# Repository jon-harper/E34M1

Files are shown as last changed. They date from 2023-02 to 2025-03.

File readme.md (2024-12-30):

Welcome to the E34M1 repository! E34M1 adapts the [EVA 3](https://main.eva-3d.page/) toolhead for the [ZeroG Mercury One](https://docs.zerog.one/) project.

This repository stores the core files for E34M1 and a number of mods. Note that many mods are published on Printables or elsewhere. A full list is available in the **[E34M1 Documentation](https://jon-harper.github.io/E34M1/)**.

## Quick Links

- [Tour](https://jon-harper.github.io/E34M1/tour/)
- [Modules & BOM](https://jon-harper.github.io/E34M1/modules/)
- [Assembly Guide](https://jon-harper.github.io/E34M1/assembly/)

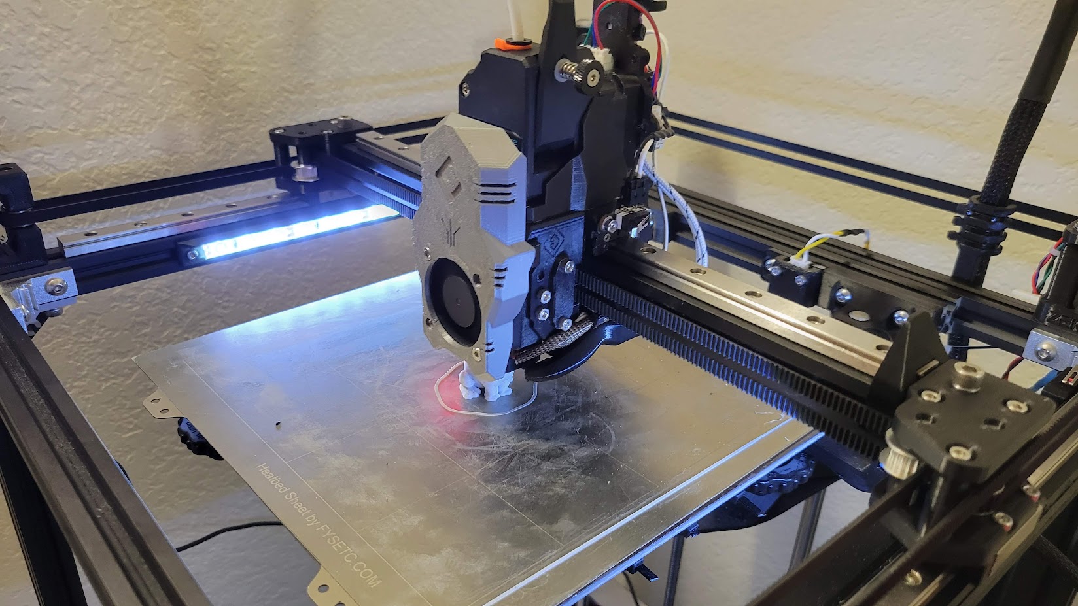
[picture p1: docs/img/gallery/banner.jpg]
E34M1 printing


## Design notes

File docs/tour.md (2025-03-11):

---
title: Visual Tour
summary: E34M1 Modules Tour
authors: Jon Harper
date: 2023-1-26
---

## Overview

Hotends, extruders, and most shrouds are compatible between EVA 3 and E34M1, but the core components of the toolhead are different. This tour introduces E34M1 and the larger EVA 3 ecosystem.

<div markdown class="grid">
<div markdown class="card">

**Core E34M1 Assembly**
<figure markdown>
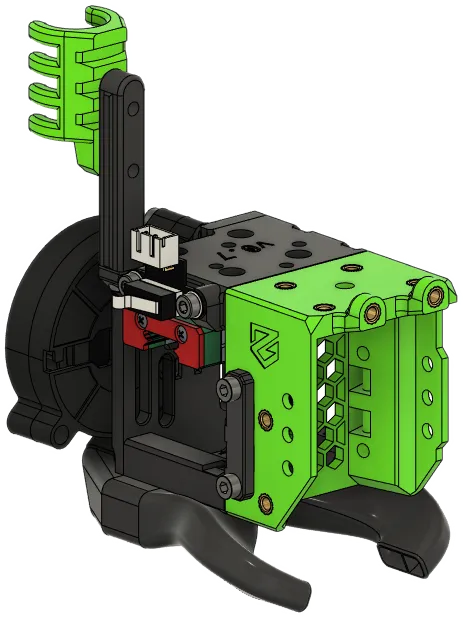
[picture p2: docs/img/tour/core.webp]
core

</figure>
</div>
<div markdown class="card">
**Complete Assembly**
<figure markdown>
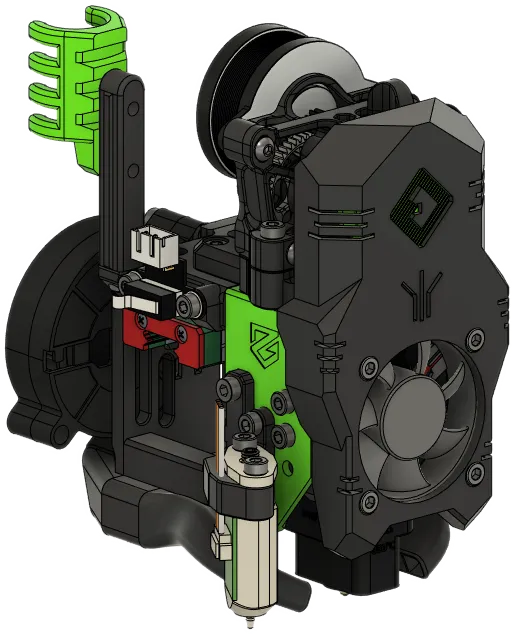
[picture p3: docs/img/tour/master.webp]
complete

</figure>
</div>
</div>

## Core Modules

Core modules are specific to E34M1. Each module comes in several variations.

<div markdown class="grid">
<div markdown class="card">

### [Front](modules/front.md)

The Front mounts the hotend, belts, the front of the Drive module, and optionally, an ABL method and/or accelerometer.

<figure markdown>
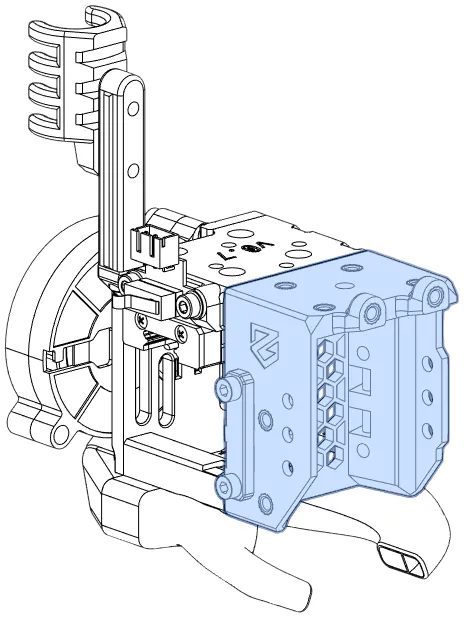
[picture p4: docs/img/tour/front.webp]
front

</figure>

</div>
<div markdown class="card">

### [Top](modules/top.md)

The top mounts the MGN12H carriage, the X endstop, and the back of the Drive module. Some Top modules have a cable guide attachment point.

<figure markdown>
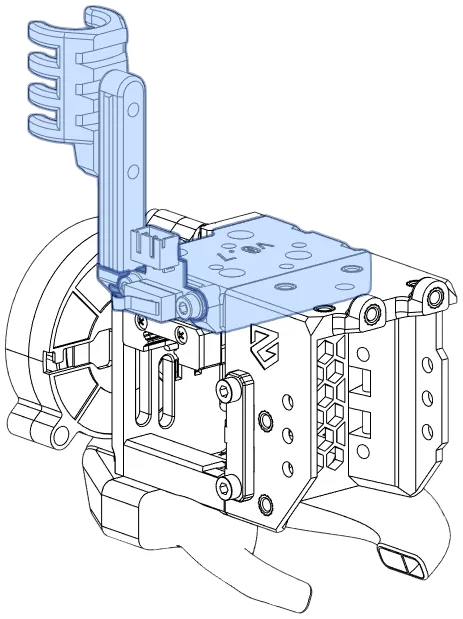
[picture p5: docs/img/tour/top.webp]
top

</figure>

</div>
<div markdown class="card">

### [Bottom Horns](modules/bottom.md)

The bottom horns form the lower joint between the Front and Rear Inlet; the horns direct part cooling air to the hotend nozzle. Some ABL methods (e.g., Beacon, Klicky) mount on the Bottom Horns.

<figure markdown>
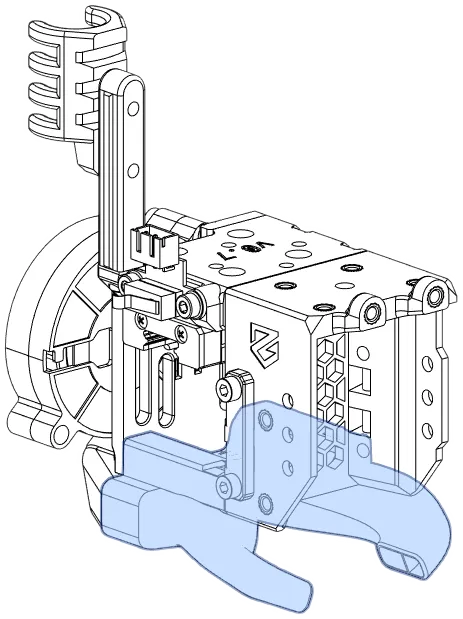
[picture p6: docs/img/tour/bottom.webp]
bottom

</figure>
</div>
<div markdown class="card">

### [Rear Inlet](modules/rear.md)

E34M1's rear body is much smaller than EVA3, and serves as a cooling fan inlet/mount.

<figure markdown>
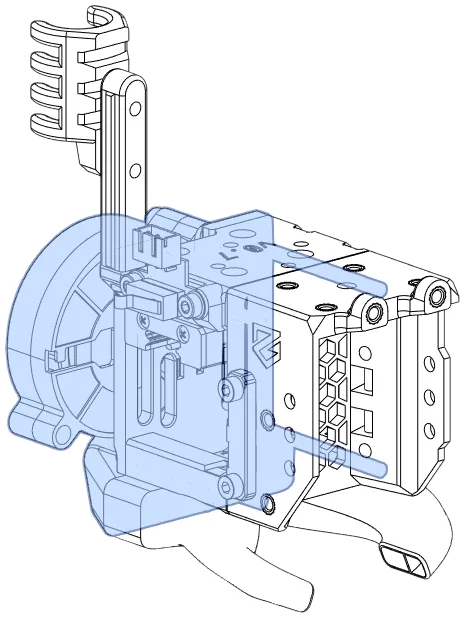
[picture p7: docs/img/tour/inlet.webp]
inlet

</figure>
</div>
<div markdown class="card">

### [ABL Side Mounts](modules/abl.md)

Some ABL methods mount here (e.g., BLTouch and CR Touch); this configuration is not compatible with EVA 3 ABL mounts.

<figure markdown>
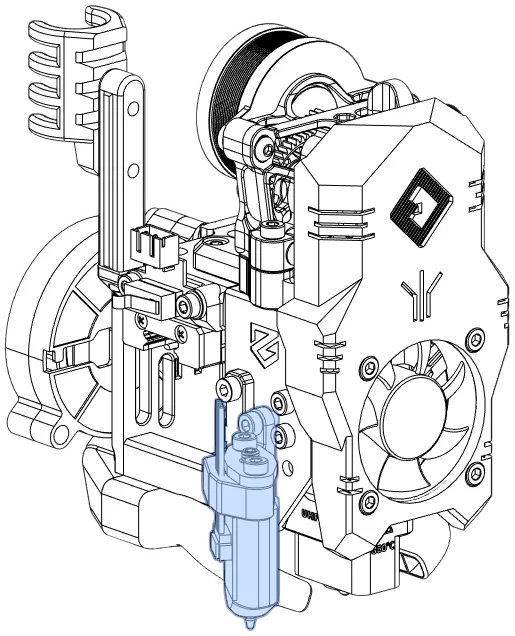
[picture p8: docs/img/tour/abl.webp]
abl mount

</figure>
</div>
</div>

## EVA-Compatible Modules

These modules are drop-in compatible with EVA 3.

<div markdown class="grid">
<div markdown class="card">

### [Hotends](modules/hotend.md)

The Hotend module mounts the hotend, cooling fan, and an optional shroud.

<figure markdown>
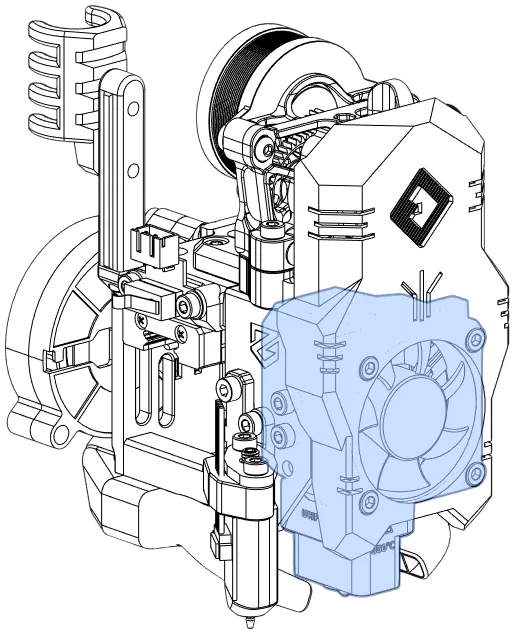
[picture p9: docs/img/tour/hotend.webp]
hotend

</figure>

</div>
<div markdown class="card">

### [Drives/Extruders](modules/drive.md)

The drive module attaches the extruder to the toolhead.

<figure markdown>
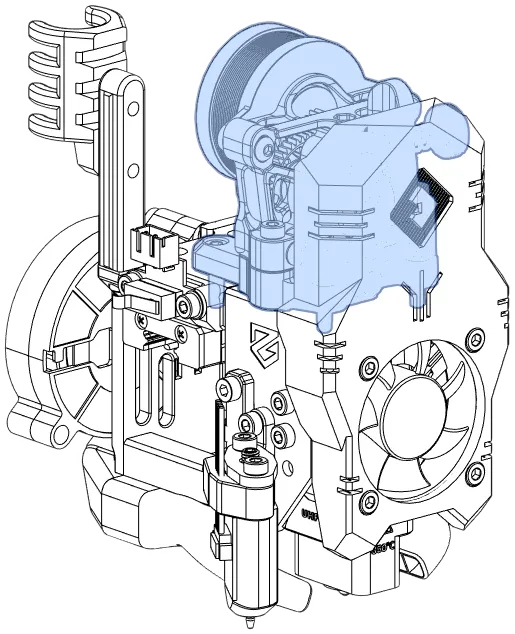
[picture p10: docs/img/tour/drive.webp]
drive

</figure>

</div>
<div markdown class="card">

### Shrouds

All stock EVA 3 shrouds are compatible with E34M1.

<figure markdown>
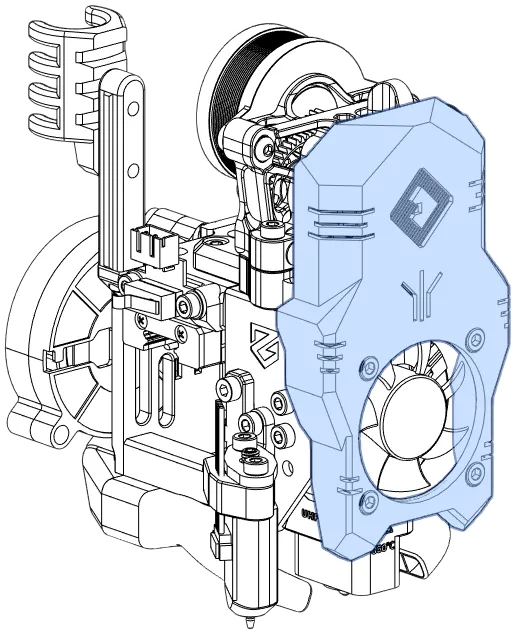
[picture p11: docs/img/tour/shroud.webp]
shroud

</figure>
- [Stock EVA 3 Shrouds](https://main.eva-3d.page/heat_insert/shrouds/chonkier/)
- [cuiviemen's Chonky Shrouds with LED Lighting](https://www.printables.com/model/420929-eva-30-chonky-shrouds-with-led-lighting)
</div>
</div>

## Other Components

E34M1 provides several other components that may be useful:

- [X Axis Stop Blocks](modules/stop_block.md): Bumpers for the X axis endstop.
- [NEMA17 PCB Mounts](modules/pcb_mounts.md): (Deprecated) NEMA17 steppers mounts for toolhead PCBs and shrouds to cover them.
- [Optional/Build-Specific](modules/other.md): Filament sensors, Klicky Docks, and other links.

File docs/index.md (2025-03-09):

---
title: The E34M1 Toolhead
summary: E34M1 landing page
authors: Jon Harper
date: 2023-1-26
hide: navigation toc
prefix: ''
---

<figure markdown class="jh-cover-img">
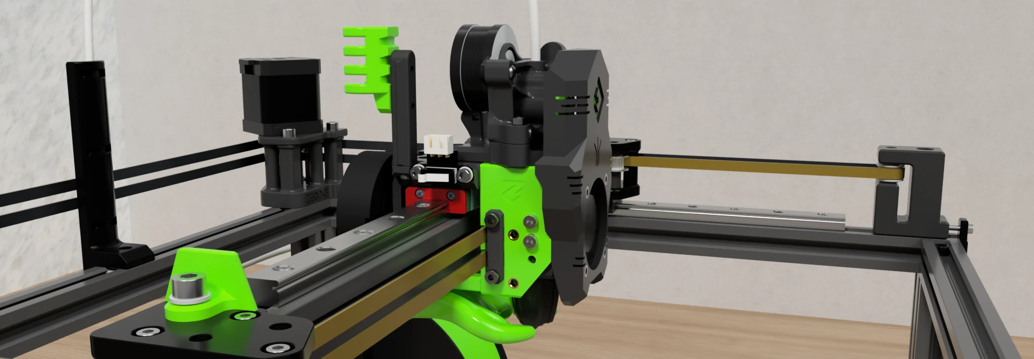
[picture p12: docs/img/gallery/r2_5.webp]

<figcaption markdown>
*E34M1 adapts the [EVA 3][eva3] toolhead
<br/> for [Mercury One.1][merc1]-based 3D printers.*
</figcaption>
</figure>

<div markdown class="grid">
<div markdown class="card">
### [:material-book-open: Introduction to E34M1](guide.md)

Overview of the toolhead and this documentation.
</div>
<div markdown class="card">
### [:material-directions: Visual Tour](tour.md)

Explore the toolhead and how it fits together.
</div>
<div markdown class="card">
### [:octicons-list-ordered-24: Sourcing Guide](sourcing.md)

Links to aid in locating and pricing parts.
</div>
<div markdown class="card">
### [:material-text-box-search-outline: Module Reference](modules/index.md)

Components, bills of materials, and notes.
</div>
<div markdown class="card">
### [:material-hammer-screwdriver: Assembly Guide](assembly/index.md)

Video and step-by-step instructions.
</div>
<div markdown class="card">
### [:octicons-log-24: Changelog](changelog.md)

What's new?
</div>
</div>

<div markdown class="grid">
<div markdown>
### License

E34M1, like [EVA 3][eva3], is licensed under the [Creative Commons BY-NC-SA 4.0 License](https://creativecommons.org/licenses/by-nc-sa/4.0/).

### Credits

E34M1 is a fork of [EVA 3][eva3] by [Paweł Kucmus](https://github.com/pkucmus). A community of makers supports E34M1, but special thanks go to [cuiviemen](https://www.printables.com/@cuiviemen_127292) and [Psych0h3ad](https://www.printables.com/@Psych0h3ad_168275) for their ideas, mod designs, testing, and feedback during development. Likewise, the testing and feedback from members of the [ZeroG Discord](https://discord.io/zerog) is invaluable.

### [:simple-kofi: Donations/Tip Jar](https://ko-fi.com/jonspaceharper)

E34M1 is free, but my Fusion 360 subscription and filament are not. Every donation helps! :material-heart:{.jh-red} *- Jon*
</div>
<div markdown>
<figure markdown class="jh-cover-img">
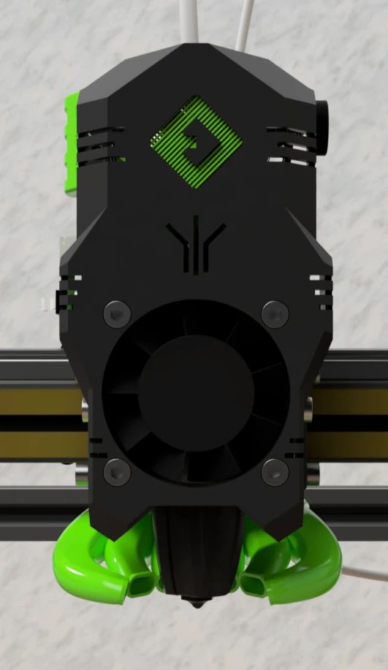
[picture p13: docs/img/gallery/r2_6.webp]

</figure>
</div>
</div>

[eva3]: https://main.eva-3d.page/
[merc1]: https://docs.zerog.one/

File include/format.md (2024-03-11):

{% import 'badges.md'as badges -%}

{% macro part_header(part_id, name) -%}
 {{ name }}
{% endmacro -%}

{% macro add_image(obj, img_width="240px", prefix = '') -%}
{% if obj.img_url -%}
{% set url = prefix + obj.img_url -%}
[{{obj.name}}}" }]({{url}})
{% endif -%}
{% endmacro -%}

{% macro add_figure(obj, img_width="240px", prefix = '') -%}
{% if obj.img_url -%}
{% set url = prefix + obj.img_url -%}
<figure markdown>
[{{obj.name}}}" }]({{url}})
</figure>
{% endif -%}
{% endmacro -%}

{%- macro add_note(comp) -%}
{% if comp.note -%}
{{ comp.note }}
{% else -%}
*(None)*
{% endif -%}
{% endmacro -%}

{%- macro add_hsi_info(item, img_width="200px", prefix='')-%}
{%- if 'hsi_img' in item.attributes.keys() %}
??? hsi "Heat Set Insert Locations"
    <div markdown class="grid">
{% for url in item.attributes['hsi_img'] %}
    [Heat set insert details}"}]({{prefix + url}})
{% endfor %}
    </div>
{% endif -%}
{%- endmacro -%}

{% macro comp_entry(comp, img_width="240px", prefix='') -%}
### {{ comp.name }}

{% if comp.attributes and comp.attributes['fit_test'] -%}

{{issue_tag(comp.attributes['fit_test'])}}
{% endif -%}

{% if comp.variants | count > 1 %}
{%- set indent='    ' -%}
{% for v in comp.variants -%}
=== "{{ v.name }}"
{{indent}}<div markdown class="grid"><div markdown>
{{indent}}{{ badges.render(comp, v, prefix=prefix) }}
{{indent}}
{{indent}}:octicons-paperclip-24: **General Notes**
{{indent}}
{{ make_indented(add_note(comp), indent) }}
{% if v.note -%}
{{indent}}:material-text-box-multiple-outline: **Variant Notes**
{{indent}}
{{ make_indented(add_note(v), indent) }}
{%- endif %}
{{indent}}</div><div markdown>
{{make_indented (add_figure(comp, img_width, prefix), indent) }}
{{indent}}</div></div>
{{indent}}:octicons-pencil-24: **Materials**
{{indent}}
{{ make_indented(bom_table(v, prefix=prefix), indent) }}
{{ make_indented(add_hsi_info(v, "200px", prefix), indent)}}
{%- endfor -%}
{%- else -%} {# comp.variants | count > 1 #}
{%- set v = comp.variants[0] -%}
<div markdown class="grid"><div markdown>
{{ badges.render(comp, v, prefix=prefix) }}

:octicons-paperclip-24: **General Notes**

{{ add_note(comp) }}

{% if v.note -%}
:material-text-box-multiple-outline: **Variant Notes**

{{add_note(v)}}
{%- endif %}
</div>
<div markdown>
{{ add_figure(comp, img_width, prefix) }}
</div>
</div>

:octicons-pencil-24: **Materials**

{{ bom_table(v, prefix=prefix) }}
{{ add_hsi_info(v, "200px", prefix) }}
{% endif -%} {# comp.variants | count > 1 #}

---------
{% endmacro -%}

{% macro source_table(part) -%}
| Source | Ships To | Ships From | Note |
|---|---|---|---|
{% if part.sources | count == 0 -%}
| | | |
{% else -%}
{% for source in part.sources -%}
| [{{source.supplier.name}}]({{source.url}} "{{source.supplier.name}}: {{part.name}}") | {{ source.supplier.ships }} | {{ source.supplier.region }} | {{ source.note }} |
{% endfor -%}
{% endif -%}
{% endmacro -%}

{% macro bom_table(variant, prefix='') -%}
| Type | Part | Qty |
|---|---|-----|
{% if variant.parts -%}
{% for part_id, qty in variant.parts.items()-%}
{% set part = product.partFromId(part_id) -%}
{% set link = part_link(part_id, part, prefix=prefix) -%}
{% if part.part_type == 'Printed' -%}
|:material-printer-3d-nozzle: {{part.part_type}}|{{link}}|{{qty}} {{part.units}}|
{% else -%}
|{{part.part_type}}|{{link}}|{{qty}} {{part.units}}|
{% endif -%}
{% endfor -%}
{% endif %}
{% endmacro -%}

{# I hate the way this macro is written, but a more concise version has newlines. #}
{% macro part_link(part_id, part = None, prefix = '', url_text=None) -%}
{% if not part -%}
{% set part = product.partFromId(part_id=part_id) -%}
{% endif -%}
{% if not url_text -%}
{% set url_text = part.name -%}
{% endif -%}
{% if not part.file_url and not part.sources -%}
{{url_text}}{% else -%}
{% if part.part_type == 'Printed' and part.file_url -%}
{% if part.file_url.startswith(product.local_url_prefix) -%}
{% set icon = ":material-git:" -%}
{% set url = part.file_url -%}
{% set tooltip = "E34M1 GitHub file download"-%}
{% else -%}
{% set icon = ':octicons-link-external-24:' -%}
{% set url = part.file_url -%}
{% set tooltip = 'External site file download'-%}
{% endif -%}
{% elif part.sources -%}
{% set icon = ':material-cart:' -%}
{% set url = prefix + 'sourcing.md#' + part_id -%}
{% set tooltip =  'Sourcing information' -%}
{% endif -%}
[{{icon}} {{url_text}}]({{url}} "{{tooltip}}"){% endif -%}
{% endmacro -%}

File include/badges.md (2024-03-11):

{%- macro template(template, prefix='') -%}
{%- if template -%}
{{ make_badge(':material-puzzle:', 'Part template', txt=template) }}
{%- endif -%}
{%- endmacro -%}

{%- macro author(name, url, prefix='') -%}
{{ make_badge(':octicons-person-fill-24:', 'Contributed by', '', name, url) }}
{%- endmacro -%}

{%- macro hsi() -%}
{{ make_badge(':material-cog:', 'Uses heat set inserts', None) }}
{%- endmacro -%}

{%- macro length(txt) -%}
{{ make_badge(':fontawesome-solid-up-down:', 'Hotend length. This affects bottom ducts and some ABL types.', txt=txt) }}
{%- endmacro -%}

{%- macro ptfe(value) -%}
{{ make_badge(':fontawesome-solid-ruler-vertical:', 'PTFE tube length needed for this part', txt=value) }}
{%- endmacro -%}

{%- macro origin(txt, txt_url) -%}
{{ make_badge(':material-source-branch:', 'Based on work by', txt=txt, txt_url=txt_url) }}
{%- endmacro -%}

{%- macro version(txt) -%}
{{ make_badge(':material-tag:', 'Version', txt=txt) }}
{%- endmacro -%}

{%- macro x_offset(txt) -%}
{{ make_badge(':material-alpha-x-box-outline:', 'Probe X axis offset', txt='{} mm'.format(txt)) }}
{%- endmacro -%}

{%- macro y_offset(txt) -%}
{{ make_badge(':material-alpha-y-box-outline:', 'Probe Y axis offset', txt='{} mm'.format(txt)) }}
{%- endmacro -%}

{%- macro render(comp, variant, prefix='') -%}
<div markdown>
{%- set ckeys = comp.attributes.keys() -%}
{%- set vkeys = variant.attributes.keys() -%}
{%- if variant.author -%}
{{ author(variant.author.name, variant.author.url, prefix) }}
{%- endif -%}
{%- if 'origin' in vkeys -%}
{%- set o_auth = authorForId(variant.attributes['origin']) -%}
{%- elif 'origin' in ckeys -%}
{%- set o_auth = authorForId(comp.attributes['origin']) -%}
{%- endif -%}
{%- if o_auth -%}
{{ origin(o_auth.name, o_auth.url) }}
{%- endif -%}
{%- if 'version' in vkeys -%}
{{ version(variant.attributes['version']) }}
{%- elif 'version' in ckeys -%}
{{ version(comp.attributes['version']) }}
{%- endif -%}
{%- if 'ptfe' in vkeys -%}
{{ ptfe(variant.attributes['ptfe']) }}
{%- elif 'ptfe' in ckeys -%}
{{ ptfe(comp.attributes['ptfe']) }}
{%- endif -%}
{%- if 'length' in vkeys -%}
{{ length(variant.attributes['length']) }}
{%- elif 'length' in ckeys -%}
{{ length(comp.attributes['length']) }}
{%- endif -%}
{%- if 'x_offset' in vkeys -%}
{{ x_offset(variant.attributes['x_offset']) }}
{%- elif 'x_offset' in ckeys -%}
{{ x_offset(comp.attributes['x_offset']) }}
{%- endif -%}
{%- if 'y_offset' in vkeys -%}
{{ y_offset(variant.attributes['y_offset']) }}
{%- elif 'y_offset' in ckeys -%}
{{ y_offset(comp.attributes['y_offset']) }}
{%- endif -%}
{%- if 'hsi' in ckeys or 'hsi' in vkeys -%}
{{ hsi() }}
{%- endif -%}
</div>
{%- endmacro -%}

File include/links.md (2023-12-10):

[x_stop_block]: https://github.com/jon-harper/E34M1/blob/main/STL/misc/x_axis_stop_block.stl
[x_max_stop_block]: https://github.com/jon-harper/E34M1/blob/main/STL/misc/x_axis_max_x_stop_block.stl
[e5plus_stop_block]: https://github.com/jon-harper/E34M1/blob/main/STL/misc/e5plus_x_axis_stop_block.stl
[z_limit_cover]: https://github.com/jon-harper/E34M1/blob/main/STL/misc/z_limit_switch_cover.stl
[z_limit_mount]: https://github.com/jon-harper/E34M1/blob/main/STL/misc/z_limit_switch_mount.stl
[cable_guide]: https://github.com/jon-harper/E34M1/blob/main/STL/misc/cable_guide.stl
[front_intake]: https://github.com/jon-harper/E34M1/blob/main/STL/misc/front_intake_duct.stl

[pcb36_mount]: https://github.com/jon-harper/E34M1/blob/main/STL/pcb/mounts/pcb36_mount.stl
[pcb42_mount]: https://github.com/jon-harper/E34M1/blob/main/STL/pcb/mounts/pcb42_mount.stl
[pcb36_mount_cable_chain]: https://github.com/jon-harper/E34M1/blob/main/STL/pcb/mounts/pcb36_mount_cable_chain.stl
[pcb42_mount_cable_chain]: https://github.com/jon-harper/E34M1/blob/main/STL/pcb/mounts/pcb42_mount_cable_chain.stl

[pcb_shroud]: https://github.com/jon-harper/E34M1/blob/main/STL/pcb/shrouds/pcb_shroud.stl
[pcb_shroud_cat]: https://github.com/jon-harper/E34M1/blob/main/STL/pcb/shrouds/pcb_shroud_cat.stl
[pcb_shroud_30mm]: https://github.com/jon-harper/E34M1/blob/main/STL/pcb/shrouds/pcb_shroud_30mm_fan.stl

[bottom_horns]: https://github.com/jon-harper/E34M1/blob/main/STL/bottom/stock_bottom.stl
[bottom_trihorns]: https://github.com/jon-harper/E34M1/blob/main/STL/bottom/stock_bottom_trihorn.stl
[bottom_uhf]: https://github.com/jon-harper/E34M1/blob/main/STL/bottom/stock_bottom_uhf.stl
[bottom_klicky]: https://github.com/jon-harper/E34M1/blob/main/STL/bottom/klicky_bottom.stl
[bottom_klicky_trihorn]: https://github.com/jon-harper/E34M1/blob/main/STL/bottom/klicky_bottom_trihorn.stl
[bottom_klicky_uhf]: https://github.com/jon-harper/E34M1/blob/main/STL/bottom/klicky_bottom_uhf.stl
[bottom_beacon]: https://github.com/jon-harper/E34M1/blob/main/STL/bottom/beacon_bottom.stl
[bottom_beacon_trihorn]: https://github.com/jon-harper/E34M1/blob/main/STL/bottom/beacon_bottom_trihorns.stl
[bottom_beacon_uhf]: https://github.com/jon-harper/E34M1/blob/main/STL/bottom/beacon_bottom_uhf.stl

[bltouch_mount]: https://github.com/jon-harper/E34M1/blob/main/STL/abl/abl_bl_touch.stl
[bltouch_volcano]: https://github.com/jon-harper/E34M1/blob/main/STL/abl/abl_bl_touch_uhf.stl
[crtouch_mount]: https://github.com/jon-harper/E34M1/blob/main/STL/abl/abl_cr_touch.stl
[crtouch_volcano]: https://github.com/jon-harper/E34M1/blob/main/STL/abl/abl_cr_touch_uhf.stl
[abl_8mm_probe]: https://github.com/jon-harper/E34M1/blob/main/STL/abl/abl_8mm_probe.stl

[front]: https://github.com/jon-harper/E34M1/blob/main/STL/front/front_adxl345.stl
[front_pis]: https://github.com/jon-harper/E34M1/blob/main/STL/front/front_fysetc_pis.stl
[front_basic]: https://github.com/jon-harper/E34M1/blob/main/STL/front/front_basic.stl
[belt_grabber]: https://github.com/jon-harper/E34M1/blob/main/STL/front/belt_grabber.stl

[top_right_endstop_anchor]: https://github.com/jon-harper/E34M1/blob/main/STL/top/top_right_endstop_anchor.stl
[top_right_endstop]: https://github.com/jon-harper/E34M1/blob/main/STL/top/top_right_endstop.stl
[top_left_endstop_anchor]: https://github.com/jon-harper/E34M1/blob/main/STL/top/top_left_endstop_anchor.stl
[top_left_endstop]: https://github.com/jon-harper/E34M1/blob/main/STL/top/top_left_endstop.stl
[cable_anchor]: https://github.com/jon-harper/E34M1/blob/main/STL/top/cable_anchor.stl
[top_no_endstop]: https://github.com/jon-harper/E34M1/blob/main/STL/top/top_no_endstop.stl

[5015_inlet]: https://github.com/jon-harper/E34M1/blob/main/STL/rear/rear_5015_inlet.stl
[rear_inlet_single_5015]: https://github.com/jon-harper/E34M1/blob/main/STL/rear/rear_inlet_single_5015.stl
[rear_intake_adapter]: https://github.com/jon-harper/E34M1/blob/main/STL/rear/stock_intake_adapter.stl
[rear_inlet_beacon]: https://github.com/jon-harper/E34M1/blob/main/STL/rear/rear_inlet_single_5015_beacon.stl
[beacon_screw_cap]: https://github.com/jon-harper/E34M1/blob/main/STL/rear/screw_cap.stl
[dual_5015_inlet]: https://github.com/jon-harper/E34M1/blob/main/STL/rear/dual_5015_inlet.stl
[rear_15mm_cpap]:  https://github.com/jon-harper/E34M1/blob/main/STL/rear/rear_inlet_15mm_cpap_beacon.stl
[rear_15mm_cpap_beacon]: https://github.com/jon-harper/E34M1/blob/main/STL/rear/rear_inlet_15mm_cpap_beacon.stl
[rear_22mm_cpap]: https://github.com/jon-harper/E34M1/blob/testing/STL/rear/rear_22mm_cpap.stl
[rear_rlf35]: https://github.com/jon-harper/E34M1/blob/main/STL/rear/rear_inlet_single_papst_rlf35.stl
[rear_rlf35_beacon]: https://github.com/jon-harper/E34M1/blob/main/STL/rear/rear_inlet_single_papst_rlf35_beacon.stl
[dual_5015_inlet_owl_eyes]: https://github.com/jon-harper/E34M1/blob/main/STL/rear/rear_dual_5015_owl_eyes.stl

[folder_cad]: https://github.com/jon-harper/E34M1/tree/main/CAD
[folder_stl]: https://github.com/jon-harper/E34M1/tree/main/STL
[repo]: https://github.com/jon-harper/E34M1

[hotend_revo_voron]: https://github.com/jon-harper/E34M1/blob/main/STL/hotend/hotend_revo_voron.stl
[hotend_dragon_bmo]: https://github.com/jon-harper/E34M1/blob/main/STL/hotend/hotend_dragon_bmo.stl
[hotend_dragonfly_bmo]: https://github.com/jon-harper/E34M1/blob/main/STL/hotend/hotend_dragonfly_bmo.stl
[hotend_dragonfly_bms]: https://github.com/jon-harper/E34M1/blob/main/STL/hotend/hotend_dragonfly_bms.stl
[hotend_rapido]: https://github.com/jon-harper/E34M1/blob/main/STL/hotend/hotend_rapido.stl
[hotend_nova]: https://github.com/jon-harper/E34M1/blob/main/STL/hotend/hotend_nova.stl
[hotend_mosquito]: https://github.com/jon-harper/E34M1/blob/main/STL/hotend/hotend_mosquito.stl
[hotend_dragon_uhf]: https://github.com/jon-harper/E34M1/blob/main/STL/hotend/hotend_dragon_uhf.stl
[hotend_rapido_uhf]: https://github.com/jon-harper/E34M1/blob/main/STL/hotend/hotend_rapido_uhf.stl

[drive_bmg]: https://github.com/jon-harper/E34M1/blob/main/STL/drives/drive_bmg.stl
[drive_lgx]: https://github.com/jon-harper/E34M1/blob/main/STL/drives/drive_lgx.stl
[drive_lgx_lite]: https://github.com/jon-harper/E34M1/blob/main/STL/drives/drive_lgx_lite.stl
[drive_orbiter_1_5]: https://github.com/jon-harper/E34M1/blob/main/STL/drives/drive_orbiter_1_5.stl
[drive_orbiter_2_0]: https://github.com/jon-harper/E34M1/blob/main/STL/drives/drive_orbiter_2_0.stl
[drive_sherpa_mini]: https://github.com/jon-harper/E34M1/blob/main/STL/drives/drive_sherpa_mini.stl

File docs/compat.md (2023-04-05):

---
title: Compatibility
summary: Summary of changes and compatibility.
authors: Jon Harper
date: 2023-1-27
---

## Mecury One Compatibility

E34M1 is compatible with Mercury One without build area limitations, i.e. no print area is lost by converting to EVA 3 from a different toolhead.

Minor modifications may be necessary to your Z axis (e.g., adjusting the Z end stop height). See [Other Changes and Additions](#other-changes-and-additions) for examples.

See the [`/CAD`][folder_cad] folder for a sample assembly in `STEP` format.

!!! note
    Mercury One.1 with E34M1 has a theoretical build area of 275mm x 275mm using 330mm linear rails.

    Practical build area is affected by your build, e.g. the type of rear intake used or presence of a toolhead PCB.

## EVA 3 Compatibility

E34M1 is generally compatible with EVA 3 hotend mounts and drive modules. Stock EVA cooling inlets may be used with E34M1 with an adapter.

### Heat Set Inserts

All E34M1 parts are designed for Mercury One/Voron-style inserts (M3x5x4) instead of the M3x4.6x4 inserts preferred by EVA. Every part has a bill of materials that reflects this.

### ABL

The side ABL mount points are different than EVA 3 stock, and not all ABL methods use them. The chart below shows which ABL methods are supported by E34M1.

| | Standard Hotends | Volcano/UHF Hotends | Mount Point |
|---|:---:|:---:|:---:|
| BLTouch  | :white_check_mark: | :white_check_mark: | ABL |
| CR Touch | :white_check_mark: | :white_check_mark: | ABL |
| Klicky | :white_check_mark: | *Planned* | Bottom |
| Beacon | :white_check_mark: | :white_check_mark: | Bottom |

Support for 8mm and 12mm inductive probes is not currently planned.

### Bottom Horns

| Duct Type | Standard Hotends | Volcano/UHF Hotends  |
|---|:---:|:---:|
| Dual Horns | :white_check_mark: | *See note* |
| Dual Horns for Klicky | :white_check_mark: | *See note* |
| Dual Horns for Beacon | :white_check_mark: | :white_check_mark: |
| Trihorns | :white_check_mark: | :x: |
| Trihorns for Klicky | :white_check_mark: | :x: |
| Trihorns for Beacon | :x: | :x: |

!!! note
    EVA 3's dual horn for Volcano hotends contains geometry errors. This limits support at present.

### Cable Management

There are two methods of cable management and two attachment points. The table below shows how they are compatible.

| Part | Cable Guide | Cable Chain |
|---|:---:|:---:|
| Top with Endstop | :white_check_mark: | *Planned* |
| PCB Mount | :white_check_mark: | :white_check_mark: |

Currently only open cable chain hole patterns are supported.

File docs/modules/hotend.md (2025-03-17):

---
title: Hotend Mounts
summary: Hotend mounts modified specifically for E34M1
authors: Jon Harper
date: 2023-4-5
prefix: '../'
---

!!! tip
    See [the end of this page](#eva-3-ecosystem-hotends) for compatible third party mounts.

{% import 'format.md' as format with context %}
{% set comp_type='Hotend' -%}

## E34M1 Native Hotends

{% set values = product.sortEntries(product.filterComponents(comp_type).values()) -%}

{% for comp in values -%}
{{ format.comp_entry(comp, prefix=prefix, img_width="200px") }}
{% endfor -%}

## Third-Party Hotends

These hotends are third-party mounts. They may use either hex nuts or heat set inserts, and may or may not include a bill of materials.

<div markdown class="jh-grid-container jh-grid-2">
<div markdown class="jh-grid-para">

### E3D Revo Micro

- **Author**: [hebijirik](https://www.printables.com/@hebijirik_84624)
- **Inserts/Hex Nuts**: hex nuts

[Files](https://www.printables.com/model/225581-eva-3-revo-micro-hotend/files){ .md-button }

</div>
<div markdown class="jh-grid-img">
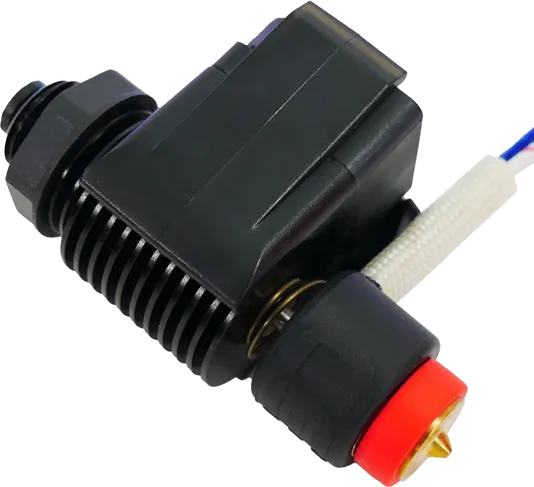
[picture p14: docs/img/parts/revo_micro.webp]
revo_micro_image

</div>
<div markdown class="jh-grid-para">

### E3D V6 & Revo V6 

- **Author**: [3DP-MAMSIH](https://www.printables.com/@3DPMAMSIH)
- **Inserts/Hex Nuts**: M3x4.6x4 inserts or hex nuts

[Files](https://www.printables.com/model/201093-eva-30-e3dv6-revo-revo-micro-hotends-mount){ .md-button }

</div>
<div markdown class="jh-grid-img">
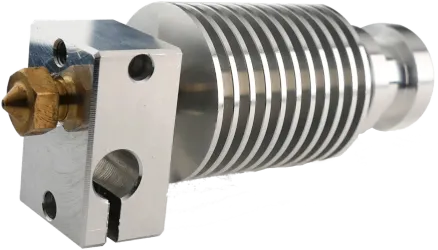
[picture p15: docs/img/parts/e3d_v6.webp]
E3D V6

</div>
<div markdown class="jh-grid-para">

### Mellow NF-Crazy

- **Author**: [Lascoose](https://www.printables.com/@Lascoose)
- **Inserts/Hex Nuts**: M3x4.6x4 inserts

[Files](https://www.printables.com/model/316658-eva-30-nf-crazy-hotend){ .md-button }

</div>
<div markdown class="jh-grid-img">
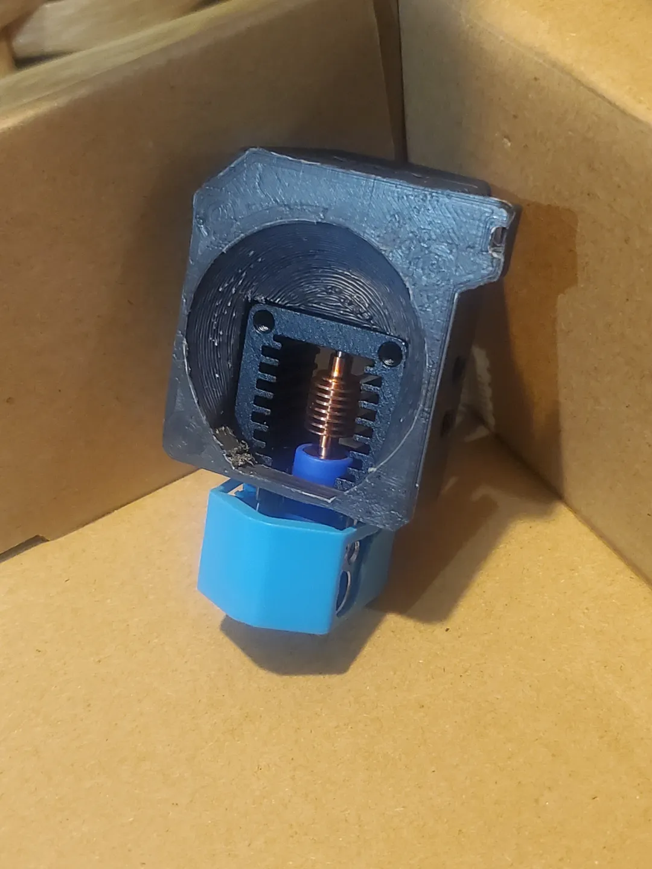
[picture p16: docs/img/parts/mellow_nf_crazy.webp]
Mellow NF-Crazy

</div>

<div markdown class="jh-grid-para">

### TriangleLabs Dragon Ace

- **Author**: [SuperHKA](https://www.printables.com/@SuperHKA_2872552)
- **Inserts/Hex Nuts**: M3x5x4 inserts

[Files](https://www.printables.com/model/1181970-dragon-ace-mount-for-e34m1){ .md-button }

### TriangleLabs TZ V6

- **Author**: [Ultrazauberer](https://www.printables.com/@Ultrazauberer_772128)
- **Inserts/Hex Nuts**: M3x5x4 inserts

[Files](https://www.printables.com/model/1227780-eva-30-e34m1-v6-tz20-hotend-mount){ .md-button }

- **Author**: [Raniel Endrino](https://www.printables.com/@RanielEndrino_310348)
- **Inserts/Hex Nuts**: M3x5x4 inserts

[Files](https://www.printables.com/model/666511-e34m1-tz2-hotend-mount-for-zerog-mercury-one1){ .md-button }

</div>

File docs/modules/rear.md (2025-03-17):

---
title: Rear Inlet
summary: Components for the Rear Module
authors: Jon Harper
date: 2023-4-5
prefix: '../'
---

{% import 'format.md' as format with context %}
{% set comp_type='Rear Inlet' -%}
{% set values = product.sortEntries(product.filterComponents(comp_type).values()) -%}

The rear module acts as a part cooling fan inlet. Use the single 5015 inlet if you
are unsure which is best.

{% for comp in values -%}
{{ format.comp_entry(comp, prefix=prefix, img_width="200px") }}
{% endfor -%}

## Third-Party Inlets

These are E34M1 mods hosted on external sites. They may or may not come with a bill of materials.

### 22mm CPAP (18mm ID)

<div markdown class="jh-grid-container jh-grid-2">
<div markdown class="jh-grid-para">

- **Author**: [Studmuffin](https://www.printables.com/@Studmuffin_2595396)
- **Inserts/Hex Nuts**: N/A

<div markdown class="jh-grid-container jh-grid-1 jh-link-grid">
[Link](https://www.printables.com/model/1176116-e34m1-18mm-cpap-rear-inlet){ .md-button}
</div>
</div>

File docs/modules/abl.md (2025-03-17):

---
title: ABL Side Mount
summary: Components for the ABL Side Mount
authors: Jon Harper
date: 2023-4-5
prefix: '../'
---

{% import 'format.md' as format with context %}
{% set comp_type='ABL Side Mount' -%}
{% set values = product.sortEntries(product.filterComponents(comp_type).values()) -%}

The side mount is used by many ABL methods and attaches to the Front. If you use Klicky, Beacon, or Cartographer, see the [Bottom Horns](bottom.md) module for mounting options.

{% for comp in values -%}
{{ format.comp_entry(comp, prefix=prefix, img_width="100px") }}

{% endfor -%}

## Third-Party Mounts

These are mounts available for E34M1 that are externally hosted. They may or may not come with a bill of materials.

### 18mm Inductive Probe

<div markdown class="jh-grid-container jh-grid-2">
<div markdown class="jh-grid-para">

- **Author**: [3D Experiments](https://www.printables.com/@3DExperiments)
- **Inserts/Hex Nuts**: N/A

<div markdown class="jh-grid-container jh-grid-1 jh-link-grid">
[Link](https://www.printables.com/model/947533-18mm-abl-probe-mount-for-e34m1-tool-head-for-zerog){ .md-button}
</div>
</div>

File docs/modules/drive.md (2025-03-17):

---
title: Extruder Mounts
summary: Extruder mounts modified for E34M1
authors: Jon Harper
date: 2023-4-19
prefix: '../'
---

!!! tip
    See [the end of this page](#eva-3-ecosystem-drives) for compatible third party mounts.

{% import 'format.md' as format with context %}
{% set comp_type='Drive' -%}

## E34M1 Native Drives

{% set values = product.sortEntries(product.filterComponents(comp_type).values()) -%}

{% for comp in values -%}
{{ format.comp_entry(comp, prefix=prefix, img_width="200px") }}
{% endfor -%}

## EVA 3 Ecosystem Drives

These are mounts from the larger EVA ecosystem that link to external sites.

### Galileo 2 StandAlone

<div markdown class="jh-grid-container jh-grid-2">
<div markdown class="jh-grid-para">

- **Author**: [cuiviemen](https://www.printables.com/@cuiviemen_127292)
- **Inserts/Hex Nuts**: M3x4.6x4 inserts

<div markdown class="jh-grid-container jh-grid-1 jh-link-grid">
[Link](https://www.printables.com/model/648710-galileo-2-sa-extruder-for-eva3){ .md-button}
</div>
</div>
<div markdown class="jh-grid-img">
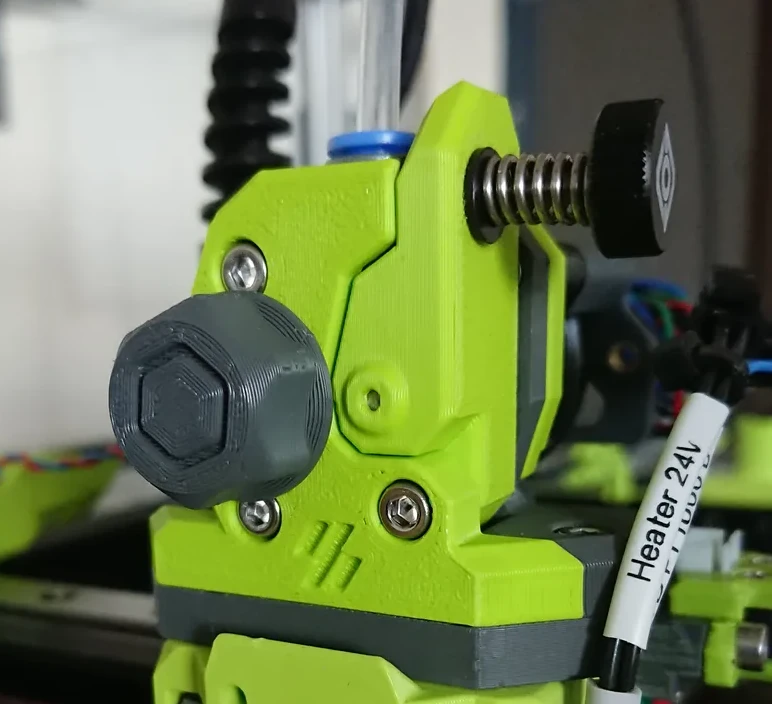
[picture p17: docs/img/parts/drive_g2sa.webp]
Galileo 2 StandAlone

</div>
</div>

### Annex Sherpa Micro

<div markdown class="jh-grid-container jh-grid-2">
<div markdown class="jh-grid-para">

- **Author**: [Psych0h3ad](https://www.printables.com/@Psych0h3ad_168275)
- **Inserts/Hex Nuts**: M3x4.6x4 inserts

<div markdown class="jh-grid-container jh-grid-1 jh-link-grid">
[Link](https://www.printables.com/model/224597-sherpa-micro-mount-for-eva-3){ .md-button}
</div>
</div>
<div markdown class="jh-grid-img">
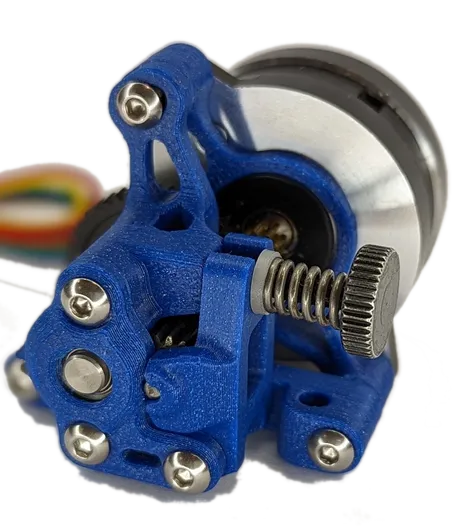
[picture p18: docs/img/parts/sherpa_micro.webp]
Annex Sherpa Micro

</div>
</div>

### E3D Titan

<div markdown class="jh-grid-container jh-grid-2">
<div markdown class="jh-grid-para">

- **Author**: [Chana Kennington](https://www.printables.com/@ChanaKenningt_484474)
- **Inserts/Hex Nuts**: None

<div markdown class="jh-grid-container jh-grid-1 jh-link-grid">
[Link](https://www.printables.com/model/424090-eva3-titan-extruder-mount){ .md-button }
</div>
</div>
<div markdown class="jh-grid-img">
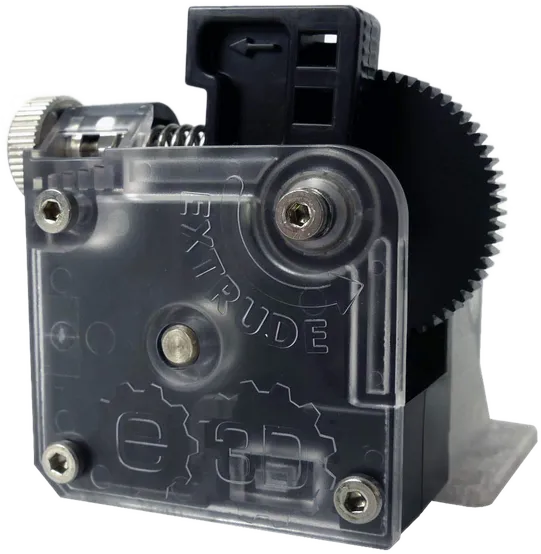
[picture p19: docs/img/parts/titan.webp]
E3D Titan

</div>
</div>

### ProtoXtruder 2.0

<div markdown class="jh-grid-container jh-grid-2">
<div markdown class="jh-grid-para">

- **Author**: [Ultrazauberer](https://www.printables.com/@Ultrazauberer_772128)
- **Inserts/Hex Nuts**: M3x5x4 inserts

<div markdown class="jh-grid-container jh-grid-1 jh-link-grid">
[Link](https://www.printables.com/model/1142327-eva-30-e34m1-protoxtruder-20-mount){ .md-button }
</div>
</div>
<div markdown class="jh-grid-img">
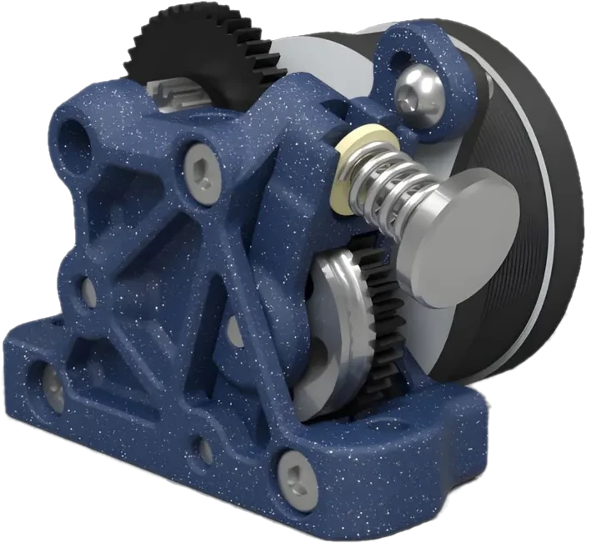
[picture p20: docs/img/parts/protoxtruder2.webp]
ProtoXtruder 2.0 Render

</div>
</div>

### VzBoT3D Vz-HextrudORT Low

<div markdown class="jh-grid-container jh-grid-2">
<div markdown class="jh-grid-para">

- **Author**: [Pr20100](https://www.printables.com/@Pr20100)
- **Inserts/Hex Nuts**: M3x4.6x4 inserts or hex nuts

<div markdown class="jh-grid-container jh-grid-1 jh-link-grid">
[Link](https://www.printables.com/model/355751-eva-3-vz-hextrudort-low-extruder-mounting-plate){ .md-button }
</div>
</div>
<div markdown class="jh-grid-img">
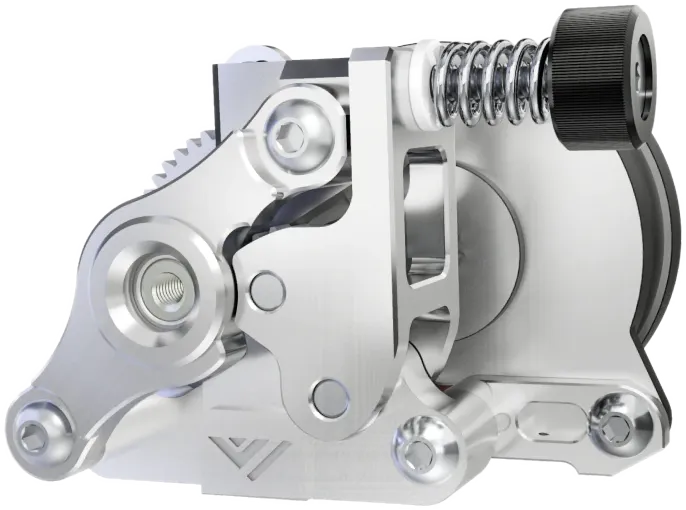
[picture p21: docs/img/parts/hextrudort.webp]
VzBoT3D Vz-HextrudORT Low

</div>
</div>

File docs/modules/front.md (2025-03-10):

---
title: Front
summary: Components for the Front Module
authors: Jon Harper
date: 2023-4-5
prefix: '../'
---

The Front module acts as a keystone or centerpiece:

- The Top, Rear, and Bottom Horns anchor to the Front, along with the hotend and some ABL methods;
- Both belts attach to the sides of the Front;
- Half of the drive module mounts above the hotend; and
- Some configurations also mount an accelerometer.

{% import 'format.md' as format with context %}
{% set comp_type='Front' -%}

{% set values = product.sortEntries(product.filterComponents(comp_type).values()) -%}

{% for comp in values -%}
{{ format.comp_entry(comp, img_width="200px", prefix=prefix) }}
{% endfor -%}

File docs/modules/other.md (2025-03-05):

---
title: Optional/Build-Specific
summary: Parts for E34M1 not part of other modules.
authors: Jon Harper
date: 2023-4-5
---

These are miscellaneous parts that may be useful in some builds.

## Additional Mods

### Klicky Docks

These are related mods not linked elsewhere that may be useful for your build.

| Mod Name | Author | Purpose |
|---|---|---|
| [Klicky Probe Dock for Mercury 1 Zero G](https://www.printables.com/model/386819-klicky-probe-dock-for-mercury-1-zero-g) | [Sir_Wash](https://www.printables.com/social/415185-sir_wash) | Adds a dock for Klicky; works with `klicky_bottom.stl`. |
| [Ender 5/Mercury One Klicky Probe Dock](https://www.printables.com/model/595738-ender-5mercury-one-klicky-probe-dock) | [jonspaceharper](https://www.printables.com/@jonspaceharper) | Uses M3 instead of M5 screws and provides enough adjustment for regular and UHF hotends. |

### Filament Sensors

Multi-material printing often requires a filament sensor at the toolhead. There are several third-party mods for this; note that these do not function as runout sensors (they are after the extruder).

- [Inductive Sensor](https://www.printables.com/model/239026-eva-3-toolhead-sensor) by [Dutchwoody](https://www.printables.com/@Dutchwoody)
- [Microswitch and Ball Bearing](https://www.printables.com/model/442650-eva-3-toolhead-sensor-mechanical-and-reliable) by [Guy](https://www.printables.com/@Guy_258839)
- [Microswitch and Ball Bearing](https://www.printables.com/model/1170113-eva-30-d2hw-filament-sensor-module/comments) by [cuiviemen](https://www.printables.com/@cuiviemen_127292)

### Z Endstop Mount

This part is necessary for Ender 5 Pros with stock (non-Hydra) Z kinematics. This part mounts the limit switch higher than normal.

<div markdown class="jh-grid-container jh-grid-2">
<div markdown class="jh-grid-para">

| Parts | Qty |
|---|-----|
| [:material-printer-3d-nozzle: `z_limit_switch_cover.stl`][z_limit_cover] | 1 |
| [:material-printer-3d-nozzle: `z_limit_switch_mount.stl`][z_limit_mount] | 1 |
| Stock Creality Endstop | 1 |
| Screw, M3-0.5 x 16mm | 2 |
| Screw, M5-0.8 x 8mm  | 1 |
| Tee Nut, Drop In, M5 | 1 |
| Heat Set Insert, M3x5x4 | 2 |

</div>
<div markdown class="jh-grid-img">
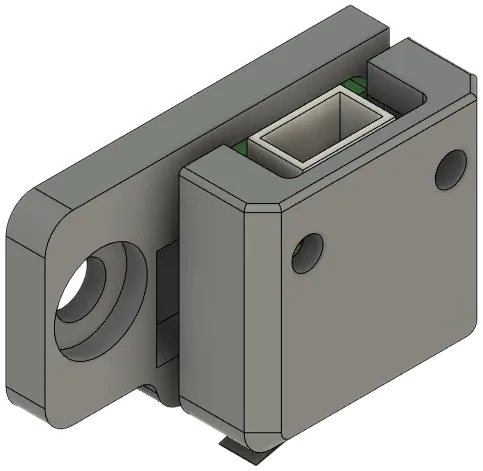
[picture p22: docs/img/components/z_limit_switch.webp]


??? info "Heat Set Insert Locations"
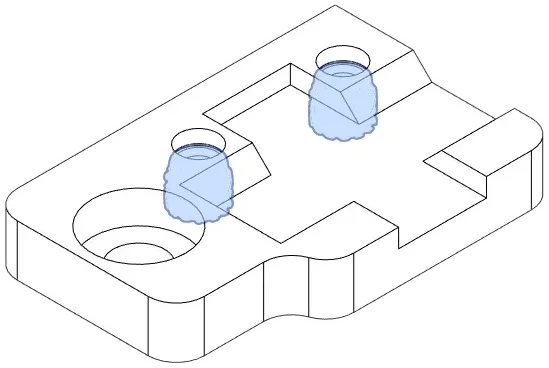
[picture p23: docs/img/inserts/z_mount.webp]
    
</div>
</div>

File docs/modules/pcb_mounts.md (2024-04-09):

---
title: Toolhead PCBs
summary: Toolhead PCB mounts and shrouds for NEMA17 steppers
authors: Jon Harper
date: 2023-4-5
---

!!! tip "Important"
    These mounts are designed for **NEMA17** steppers. There are several off-the-shelf options for **NEMA14** steppers:

    - ZeroG Discord members can use TurtleCrawler's [CANbus 36 mounts](https://discord.com/channels/747612067951018075/1058784239539191838/1058784239539191838)
    - [https://github.com/KayosMaker/CANboard_Mounts](https://github.com/KayosMaker/CANboard_Mounts)

!!! warning "Warning: Deprecated"
    The files on this page are deprecated and may be removed in the future.

This page contains parts for mounting toolhead PCBs on the back of a NEMA17 stepper. Optional shrouds are used to cover the PCB wiring.

The first half of this page contains mounts for both NEMA14 ("36") and NEMA17 ("42") PCBs. Examples of '36 PCBs are the BIGTREETECH EBB36 and  Mellow Fly SHT36. An example of a '42 PCB is the BIGTREETECH EBB42. Variants of each mount are available for both cable guides and drag chains.

## PCB Mounts

### '36 PCB, Cable Guide
<div markdown class="jh-grid-container jh-grid-2">
<div markdown class="jh-grid-para">

**Description**

Mounts a '36 toolhead PCB with anchor points a cable guide. Meant for umbilical users.

**Bill of Materials**

| Parts | Qty | Notes |
|---|-----|---|
| [:material-printer-3d-nozzle: `pcb36_mount.stl`][pcb36_mount] | 1 | |
| [:material-printer-3d-nozzle: `cable_guide.stl`][cable_guide] | 1 | |
| Toolhead PCB | 1 | |
| Screw, M3-0.5 x 25mm | 2 | |
| Screw, M3-0.5 x 6mm  | 4 | May substitute two (2) 8mm screws, if desired. |
| Heat Set Insert, M3x5x4 | 6 | |

</div>
<div markdown class="jh-grid-img">
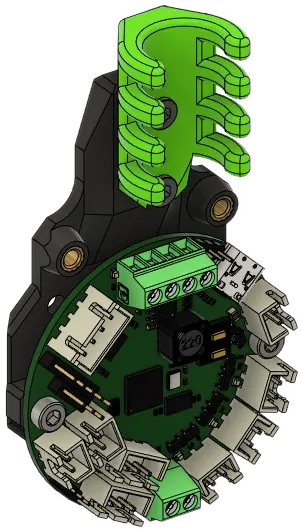
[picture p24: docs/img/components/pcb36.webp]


??? info "Heat Set Insert Locations"
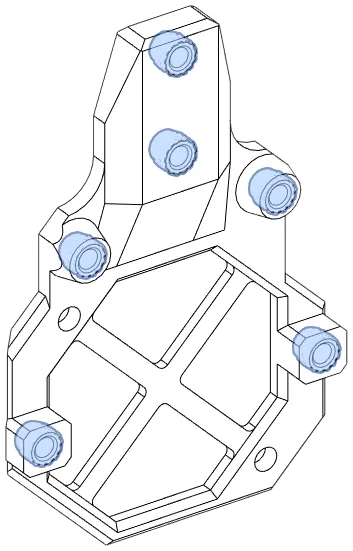
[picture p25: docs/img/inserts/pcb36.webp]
    
</div>
</div>

### '36 PCB, Drag Chain

<div markdown class="jh-grid-container jh-grid-2">
<div markdown class="jh-grid-para">

**Description**

Mounts a '36 toolhead PCB with anchor points for an open drag chain.

**Bill of Materials**

| Parts | Qty | Notes |
|---|-----|---|
| [:material-printer-3d-nozzle: `pcb36_mount_cable_chain.stl`][pcb36_mount_cable_chain] | 1 | |
| Toolhead PCB | 1 | |
| Screw, M3-0.5 x 25mm | 2 | |
| Screw, M3-0.5 x 6mm  | 5 | May substitute 8mm screws, if desired. |
| Heat Set Insert, M3x5x4 | 7 | |

</div>
<div markdown class="jh-grid-img">
pcb36_illustration

??? info "Heat Set Insert Locations"
    pcb36_illustration
</div>
</div>

### '42 PCB, Cable Guide

<div markdown class="jh-grid-container jh-grid-2">
<div markdown class="jh-grid-para">

**Description**

Mounts a '42 toolhead PCB with anchor points a cable guide. Meant for umbilical users.

**Bill of Materials**

| Parts | Qty | Notes |
|---|-----|---|
| [:material-printer-3d-nozzle: `pcb42_mount.stl`][pcb42_mount] | 1 | |
| [:material-printer-3d-nozzle: `cable_guide.stl`][cable_guide] | 1 | |
| Toolhead PCB | 1 | |
| Screw, M3-0.5 x 25mm | 2 | |
| Screw, M3-0.5 x 6mm  | 4 | May substitute two (2) 8mm screws, if desired. |
| Heat Set Insert, M3x5x4 | 6 | |

</div>
<div markdown class="jh-grid-img">
pcb42_illustration

??? info "Heat Set Insert Locations"
    pcb42_illustration
</div>
</div>

### '42 PCB, Drag Chain

<div markdown class="jh-grid-container jh-grid-2">
<div markdown class="jh-grid-para">

**Description**

Mounts a '42 toolhead PCB with anchor points for an open drag chain.

**Bill of Materials**

| Parts | Qty | Notes |
|---|-----|---|
| [:material-printer-3d-nozzle: `pcb42_mount_cable_chain.stl`][pcb42_mount_cable_chain] | 1 | |
| Toolhead PCB | 1 | |
| Screw, M3-0.5 x 25mm | 2 | |
| Screw, M3-0.5 x 6mm  | 5 | May substitute 8mm screws, if desired. |
| Heat Set Insert, M3x5x4 | 7 | |

</div>
<div markdown class="jh-grid-img">
pcb42_illustration

??? info "Heat Set Insert Locations"
    pcb42_illustration
</div>
</div>

## PCB Shrouds

These shrouds cover the PCB and wiring for a PCB mount. The 30mm fan is strongly encouraged for enclosed builds.

PCB shrouds come in three styles:

- Stock
- Cat face
- 30mm Fan

The cat face shroud is purely cosmetic and uses the same materials as the stock shroud.

### Basic

<div markdown class="jh-grid-container jh-grid-2">
<div markdown class="jh-grid-para">

| Parts | Qty |
|---|-----|
| [:material-printer-3d-nozzle: `pcb_shroud.stl`][pcb_shroud] or [:material-printer-3d-nozzle: `pcb_shroud_cat.stl`][pcb_shroud_cat]| 1 |
| Screw, M3-0.5 x 35mm | 2 |

</div>
<div markdown class="jh-grid-img">
pcb42_illustration
</div>
</div>

### 30mm Fan

<div markdown class="jh-grid-container jh-grid-2">
<div markdown class="jh-grid-para">

| Parts | Qty |
|---|-----|
| [:material-printer-3d-nozzle: `pcb_shroud.stl`][pcb_shroud_30mm] | 1 |
| Screw, M3-0.5 x 35mm | 2 |
| Axial Fan, 30mm x 10mm | 1 |
| Screw, M3-0.5 x 16mm | 2 |
| Heat Set Insert, M3x5x4 | 4 |

</div>
<div markdown class="jh-grid-img">
pcb42_illustration
</div>
</div>

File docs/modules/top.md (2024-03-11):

---
title: Top
summary: Components for the Top Module
authors: Jon Harper
date: 2023-4-5
prefix: '../'
---

{% import 'format.md' as format with context %}
{% set comp_type='Top' -%}
{% set values = product.sortEntries(product.filterComponents(comp_type).values()) -%}

The Top module attaches to the MGN12H carriage and mounts the X axis endstop. The right-handed versions home to the right, and vice versa for the left. Both left- and right-handed versions are available with and without a built-in anchor for a cable guide.

!!! tip
    Don't forget to grab the [X Axis Stop Block](stop_block.md)!

{% for comp in values -%}
{{ format.comp_entry(comp, prefix=prefix, img_width="200px") }}

{% endfor -%}

### Integrated Microswitch

There are two known Top mods that use a simple microswitch (e.g. Omron D2F-L).

<div markdown class="grid">
<div markdown class="card">
top_syph3rd (https://www.printables.com/@syph3rd_963296)

[Top MGN12H with Inbuilt Limit](https://www.printables.com/model/555302-zero-g-mercury-e34m1-top-mgn12h-with-inbuilt-limit) by [syph3rd](https://www.printables.com/@syph3rd_963296)
</div>
<div markdown class="card">
top_heinlein (https://www.printables.com/model/658976-zero-g-mercury-e34m1-top-mgn12h-with-integrated-li) by [Christopher Heinlein](https://www.printables.com/@ChristopherHe_488911)

[Top MGN12H with Integrated Limit Switch (remix)](https://www.printables.com/model/658976-zero-g-mercury-e34m1-top-mgn12h-with-integrated-li) by [Christopher Heinlein](https://www.printables.com/@ChristopherHe_488911)
</div>
</div>

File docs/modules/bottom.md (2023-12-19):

---
title: Bottom Horns
summary: Components for the Bottom Horns Module
authors: Jon Harper
date: 2023-4-5
prefix: '../'
---

{% import 'format.md' as format with context %}
{% set comp_type='Bottom Horns' -%}
{% set values = product.sortEntries(product.filterComponents(comp_type).values()) -%}

Your duct should match the length of your hotend. If you are using Beacon or Klicky, choose
the appropriate variant for that ABL method.

See the Intro Guide's [compatibility](../guide.md#bottom-horns) section for more information and
a table of hotends and ducts.

{% for comp in values -%}
{{ format.comp_entry(comp, prefix=prefix, img_width="200px") }}
{% endfor -%}

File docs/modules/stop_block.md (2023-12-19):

---
title: X Axis Stop Blocks
summary: Options for triggering the X endstop.
authors: Jon Harper
date: 2023-5-3
prefix: '../'
---

{% import 'format.md' as format with context %}
{% set comp_type='X Stop Block' -%}
{% set values = product.sortEntries(product.filterComponents(comp_type).values()) -%}

Stop blocks are bumpers for the X endstop (or toolhead if using sensorless homing). Several options are available based on your needs.

{% for comp in values -%}
{{ format.comp_entry(comp, prefix=prefix, img_width="200px") }}

{% endfor -%}

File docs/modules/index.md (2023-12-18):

---
title: Modules Overview
summary: Overview of component entries
authors: Jon Harper
date: 2023-4-5
hide: toc
---

This section of the documentation contains a page for each E34M1 module and the components available for them.
Each component, and its variations, contains a bill of materials and other key information.

<div markdown class="grid cards">

- ## Core Modules

    - [Front](front.md)
    - [Top](top.md)
    - [Rear Inlet](rear.md)
    - [Bottom Horns](bottom.md)
    - [ABL Side Mount](abl.md)

- ## Universal Modules

    These modules are compatible with stock EVA 3.

    - [Hotend Mounts](hotend.md)
    - [Extruder Mounts](drive.md)

- ## Additional Modules

    - [X Axis Stop Blocks](stop_block.md)
    - [Toolhead PCB Mounts and Shrouds](pcb_mounts.md)
    - [Optional & Build Specific](other.md)
</div>

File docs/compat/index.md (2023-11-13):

---
title: Introduction to E34M1
summary: Summary of changes and compatibility.
authors: Jon Harper
date: 2023-1-27
---

## Mercury One Compatibility

E34M1 is compatible with Mercury One.1 without limiting the build area; no print area is lost with stock beds by converting to EVA 3 from a different toolhead. In some configurations, minor adjustments to the Z axis are needed. See [Other Changes and Additions](#other-changes-and-additions) for examples.

An Ender 5 Pro rebuilt as a Mercury One.1 with 330mm rails:

- Has a *theoretical* build area of 275mm x 275mm;
- Can expect at least 265mm of X axis travel;
- Can expect at least 250mm of Y axis travel, typically more.

!!! note
    E34M1 is *not* compatible with Mercury One Classic.

!!! tip
    Making a mod? Want to see how it looks in CAD? See the [`/CAD`][folder_cad] folder for a `STEP` files.

## Icons and Terminology

These terms and icons are used throughout the site.

- The :material-printer-3d-nozzle: icon is used to emphasize that a part is 3D printed.
- The :material-cart: shopping cart icon is for example links. *There are no affiliate links on this site.*
- Drive: EVA 3 refers to the extruder, stepper, and mount as the *Drive* module.
- FHCS: flat head cap screw (DIN 7991)
- SHCS: socket head scap screw (DIN 912)
- Voron-style inserts: M3 x 5mm OD x 4mm L heat set inserts
- EVA-style inserts: M3 x 4.6mm OD x 4mm L heat set inserts

## Frequently Asked Questions

### How does this fit together?

Visit the [Tour](../tour.md) to get an overview of how the modules are arranged. The [Assembly Guide](../assembly/index.md) includes videos to assist during your build process.

### What do I print?

See the Assembly guide's [Print Checklist](../assembly/#print-checklist) to ensure you have everything.

### What does an *italic* BOM entry mean?

These are optional parts that may be included or left out, at your discretion.

### How are Voron-style and EVA-style inserts different?

Both insert styles are M3 and 4mm long, but Voron-style inserts are slightly thicker than EVA inserts. Mercury One relies on Voron-style inserts exclusively, so all E34M1 components use them, as well. Third-party and stock EVA components use EVA-style inserts instead.

Does it matter? Somewhat: the adjustments we made for the larger, Voron-style inserts make insertion easier and visually cleaner. Users report that it is generally still possible to use Voron-style inserts with parts made for EVA inserts.

### Is E34M1 supported by ZeroG or EVA?

No, this is a third-party project started by [jonspaceharper](https://jon-harper.github.io).

## Compatibility Charts

Some components are only compatible in certain combinations. This generally relates to whether a part is for a standard-length or UHF-length hotend.

### ABL

The chart below shows which ABL methods are supported by E34M1. The side ABL mount points are different than EVA 3 stock, and not all ABL methods use them.

| | Standard Hotends | UHF Hotends | Mount Point |
|---|:---:|:---:|:---:|
| 8mm Probes | :white_check_mark: | :white_check_mark: | ABL |
| 12mm Probes | :x: | :x: | ABL |
| Beacon | :white_check_mark: | :white_check_mark: | Bottom/Rear |
| BL-Touch | :white_check_mark: | :white_check_mark: | ABL |
| CR-Touch | :white_check_mark: | :white_check_mark: | ABL |
| Klicky | :white_check_mark: | :white_check_mark: | Bottom |
| Klicky PCB | :x: | :x: | ABL |

### Bottom Horns

Most hotends are paired with the basic Dual Horns. Very long hotends, such as the Rapido UHF, require the UHF bottom horns. The Mosquito has its own bottom horns as a cooling workaround.

More about Bottom Horns can be found on the [Bottom Horns Modules](../modules/bottom.md) page.

| Hotend | Bottom Horns  |
|---|:---:|
| 3D Passion Nova | Dual |
| E3D Revo Voron | Dual |
| Phaetus Dragonfly BMO | Dual |
| Phaetus Dragonfly BMS | Dual |
| Phaetus Dragon BMO | Dual |
| Phaetus Dragon UHF | Dual |
| Phaetus Rapido | Dual |
| Phaetus Rapido UHF | UHF |
| Slice Engineering Mosquito | Trihorn  |

### Cable Management

There are two methods of cable management. The default attachment is the [Top](../modules/top.md) module for umbilical users. Third parties offer PCB mounts supporting both umbilical (cable guide) and drag chains.

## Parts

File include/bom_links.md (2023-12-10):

[bom_m3x6_fhcs]: https://www.boltdepot.com/Metric_socket_flat_head_Stainless_steel_18-8_(A-2)_6mm_x_1.0mm.aspx
[bom_limit_switch]: https://www.amazon.com/REIFENG-Mechanical-Vertical-Printers-Accessories/dp/B08CDF3Q6T/
[bom_inserts]: https://www.amazon.com/uxcell-Knurled-Insert-Female-Embedding/dp/B09MCWTBCC
[bom_papst_rlf35]: https://www.ebmpapst.com/at/en/products/centrifugal-fans/p/RLF35814N.html

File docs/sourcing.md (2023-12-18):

---
title: Sourcing Guide
summary: List of parts and known sources.
authors: Jon Harper
date: 2023-11-30
prefix: ''
---

Need help sourcing parts?

!!! note
    - This page is not an endorsement for any product or reseller.
    - Not all parts are verified.
    - Amazon and AliExpress links use manufacturer stores, where possible.
    - No affiliate links are included.

{% import 'format.md' as fmt with context %}

{% for part_type in product.part_types | sort -%}

{% if part_type != 'Printed' -%}

### {{ part_type }}

{% for part_id, part in product.sortKeyEntries(product.filterParts(part_type).items()) -%}

#### {{ fmt.part_header(part_id, part.name) }}

<div markdown class="jh-grid-container jh-grid-2">
<div markdown class="jh-grid-para">
{% if part.note -%}
!!! note 
    {{ part.note }}

{% endif -%}
{{ fmt.source_table(part) }}
</div>
{% if part.img_url -%}
<div markdown class="jh-grid-img">
{{part.name}}
</div>
{% endif -%}
</div>
{% endfor %}

{% endif -%}

{% endfor %}

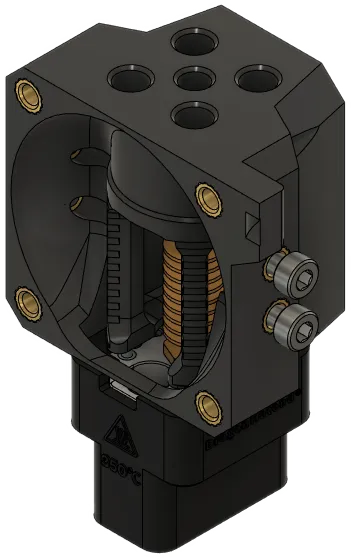
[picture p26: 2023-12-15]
docs/img/components/hotend_dragon_uhf.webp

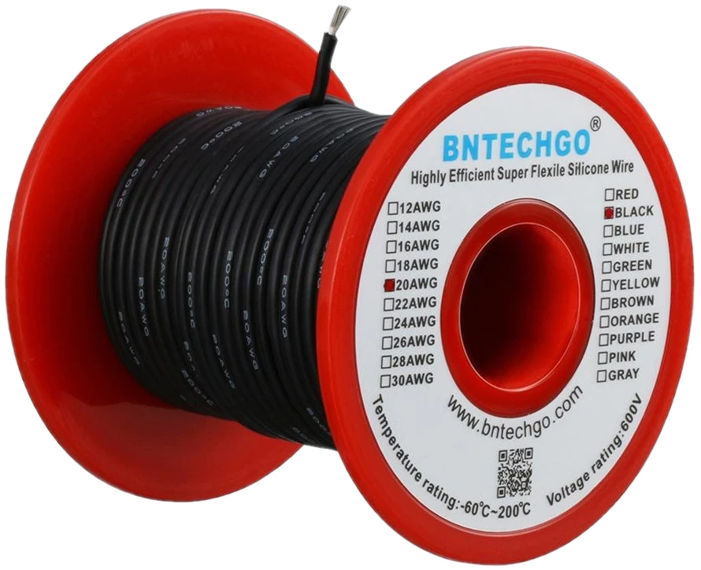
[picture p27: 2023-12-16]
docs/img/parts/wire_20awg.webp

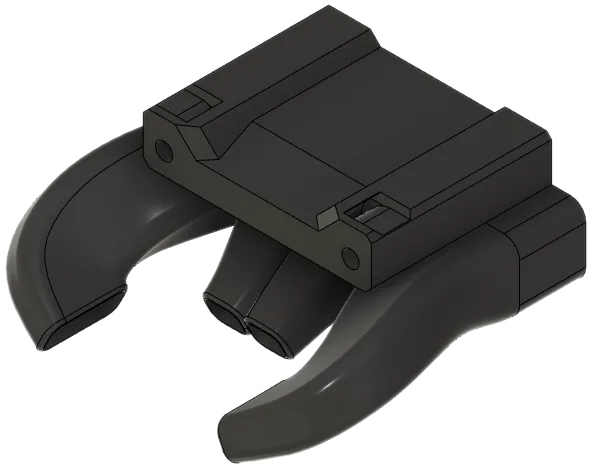
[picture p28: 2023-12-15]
docs/img/components/bottom_trihorns.webp

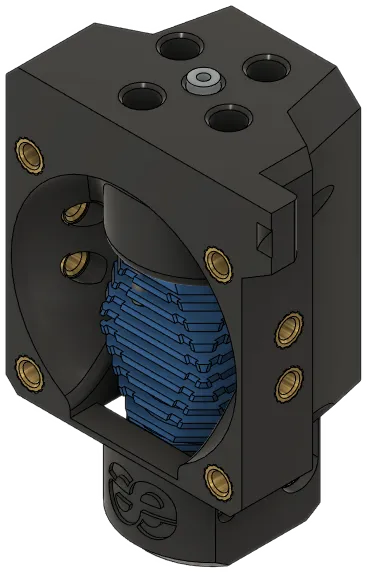
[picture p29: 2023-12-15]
docs/img/components/hotend_dragonfly_bmo.webp

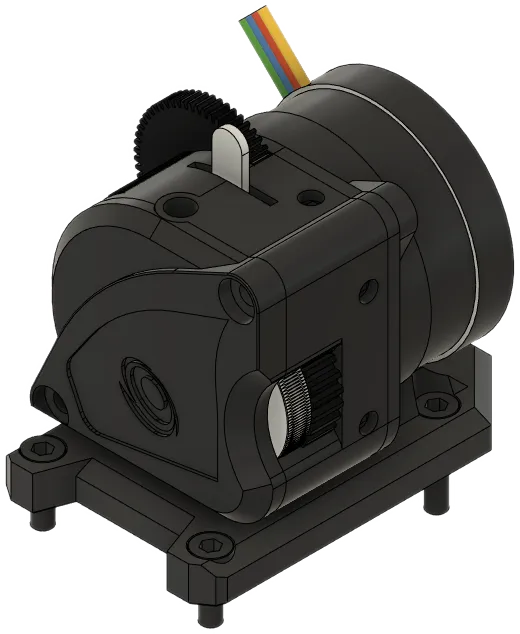
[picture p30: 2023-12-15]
docs/img/components/lgx_lite.webp

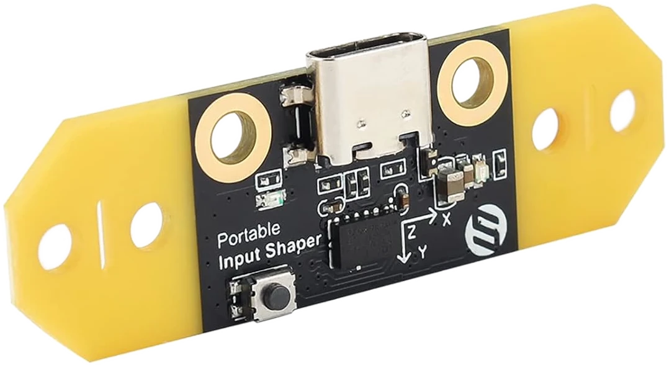
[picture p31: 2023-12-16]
docs/img/parts/fysetc_pis.webp

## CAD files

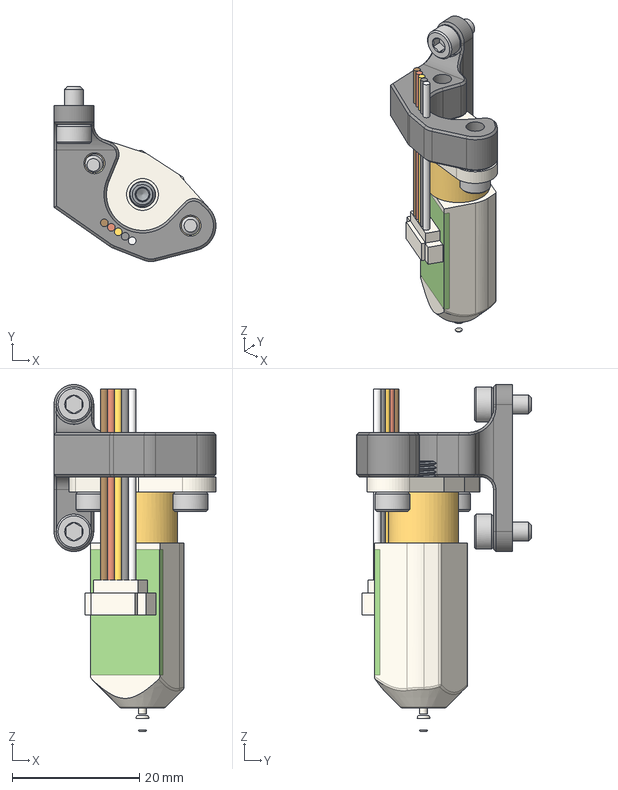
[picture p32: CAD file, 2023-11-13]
CAD/abl/abl_bl_touch_uhf.step
25.5 x 27.5 x 54.5 mm
PN485
abl_bl_touch_uhf_1
PN596 x 2
Screw, M3 x 6mm, SHCS x 4

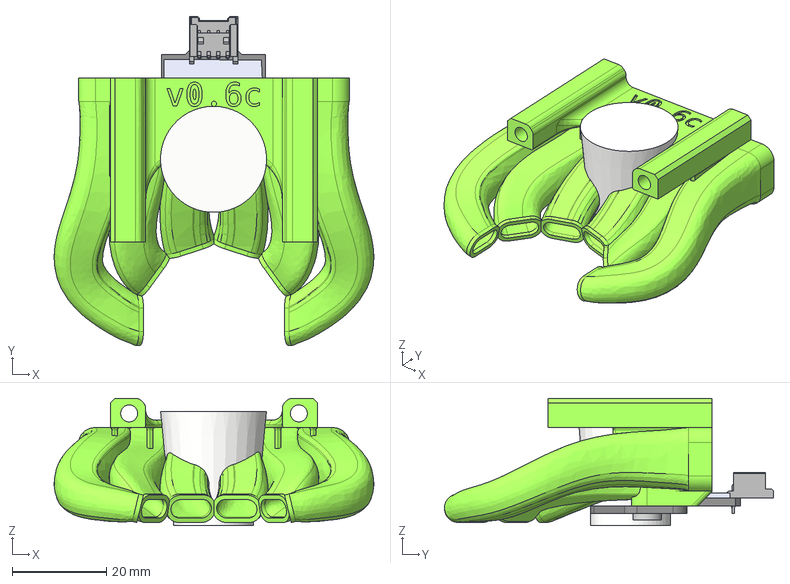
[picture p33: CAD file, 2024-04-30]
CAD/bottom/kraken_beacon.step
67.8 x 69.8 x 27.0 mm
kraken
PN596 x 2
Controller_PCB
Coil_PCB
Clearances
BN 1206 3555982 hex socket head cap screw M3x4 x 2

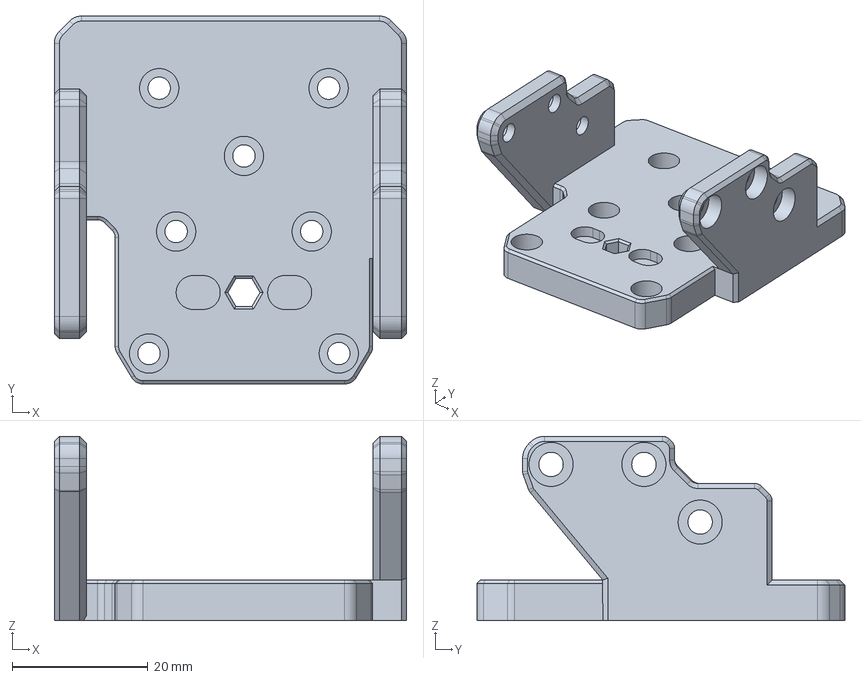
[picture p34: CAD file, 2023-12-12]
CAD/drive/drive_creality_sprite_se.step
52.0 x 54.3 x 27.2 mm

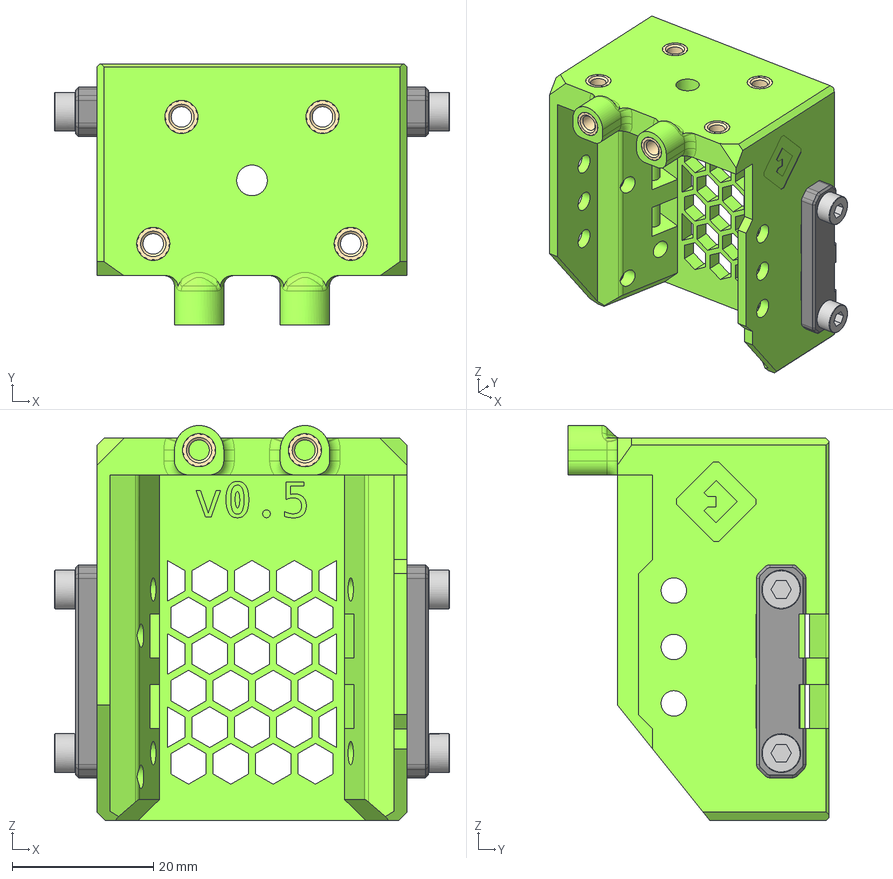
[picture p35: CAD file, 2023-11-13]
CAD/front/front_adxl_345.step
56.0 x 37.0 x 56.0 mm
PN596 x 16
PN501 x 4
belt_grabber x 2
front_adxl345

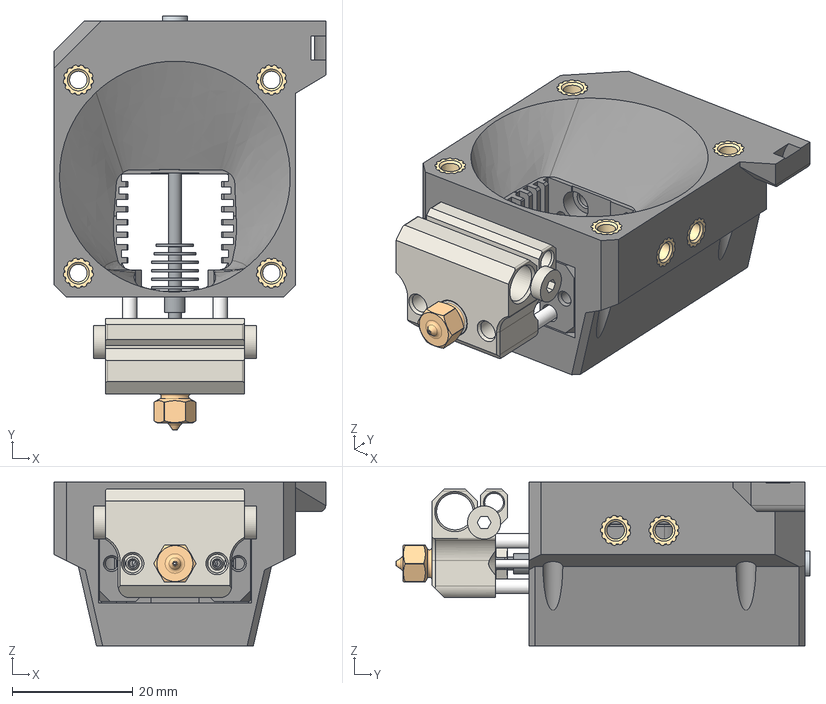
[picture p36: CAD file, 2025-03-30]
CAD/hotend/hotend_mosquito_osr.step
45.0 x 68.6 x 27.2 mm
mosquito_2
mosquito (1)
mosquito (23)
mosquito (20)
mosquito (22)
mosquito (2)
mosquito (3)
mosquito (4)
mosquito (5)
mosquito (6)
mosquito (7)
mosquito (8)
mosquito (9)
mosquito (10)
mosquito (11)
mosquito (12)
mosquito (13)
mosquito (14)
mosquito (15)
mosquito (16)
mosquito (17)
mosquito (21)
mosquito (18)
mosquito (19)
hotend_mosquito
PTFE_22.6_mm
PN596 x 8
91292A012_18-8 Stainless Steel Socket Head Screw x 2

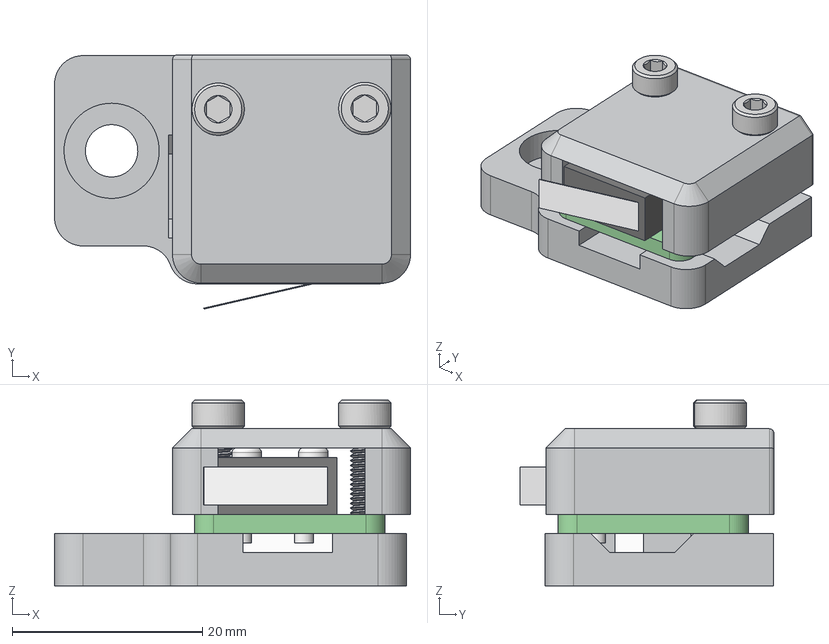
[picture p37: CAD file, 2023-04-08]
CAD/misc/Z Limit Switch.step
37.4 x 26.7 x 19.5 mm
Limit Switch Plate
Limit Switch
PN091
PN596 x 2
PN503 x 2

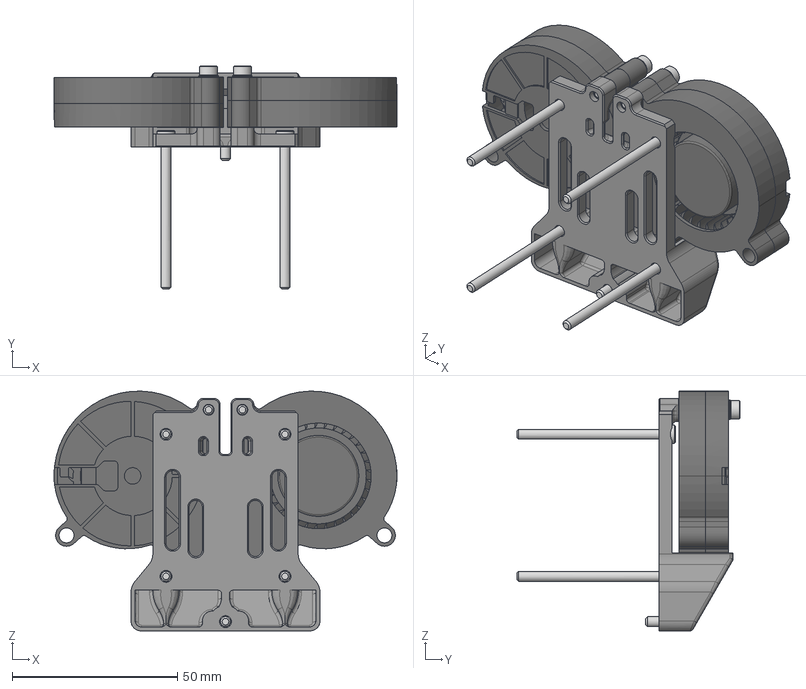
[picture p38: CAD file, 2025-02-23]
CAD/rear/rear_dual_5015_owl_eyes_beacon.step
103.8 x 67.6 x 72.6 mm
rear_dual_5015_owl_eyes
turbine x 2
top x 2
bottom x 2
PN596 x 2
Screw, M3 x 45mm, SHCS x 4
Screw, M3 x 6mm, SHCS
Washer, M3 x 6mm x 2
Screw, M3 x 20mm, SHCS x 2

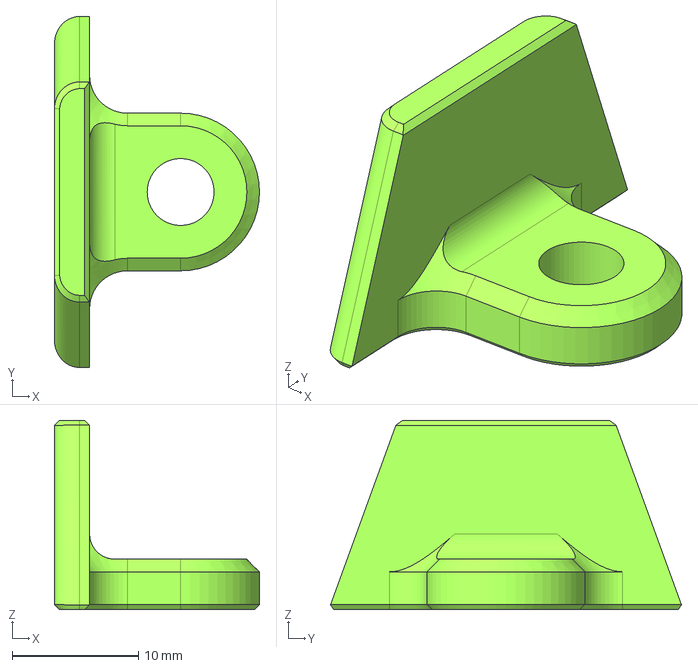
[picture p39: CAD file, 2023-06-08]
CAD/stop block/X Max Stop Block.step
16.2 x 27.8 x 15.0 mm

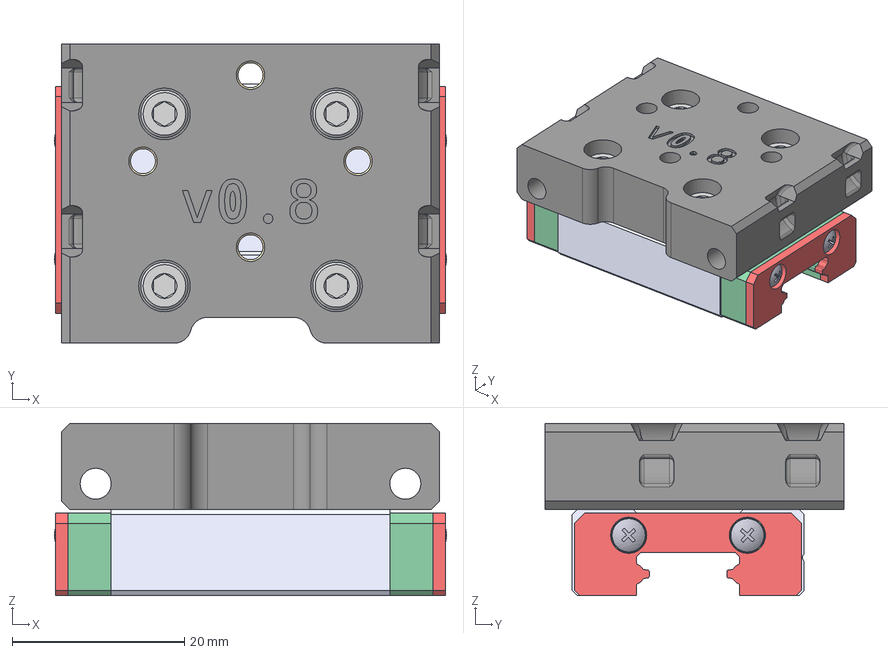
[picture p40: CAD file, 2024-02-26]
CAD/top/top_no_endstop.step
45.6 x 34.8 x 20.0 mm
top_no_endstop_1
PN596 x 4
91292A112_18-8 Stainless Steel Socket Head Screw x 4
PN632

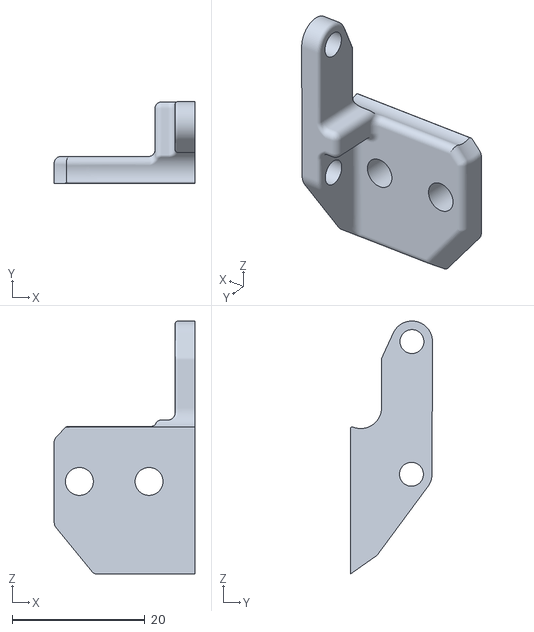
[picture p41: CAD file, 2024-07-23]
STL/abl/abl_eddy.stl
21.2 x 12.4 x 38.1

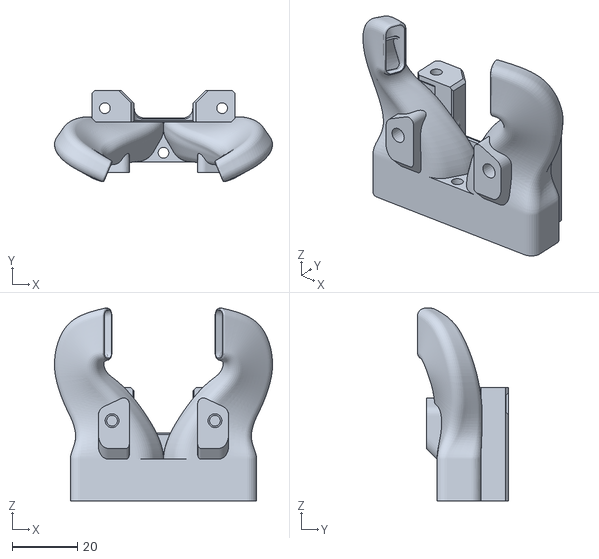
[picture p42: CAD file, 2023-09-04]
STL/bottom/beacon_bottom.stl
66.9 x 28.1 x 59.2

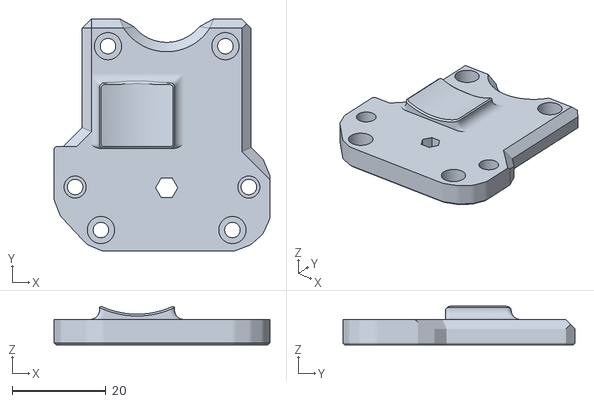
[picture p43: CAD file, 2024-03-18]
STL/drives/drive_orbiter_2_0.stl
46.0 x 49.5 x 8.20

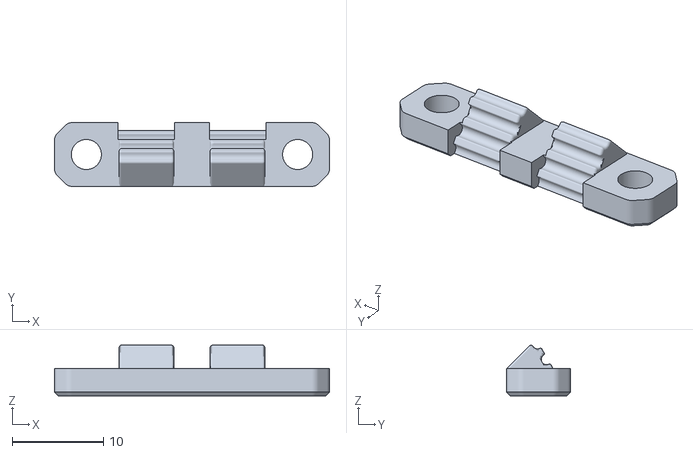
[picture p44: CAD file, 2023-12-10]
STL/front/belt_grabber.stl
30.2 x 7.00 x 5.57

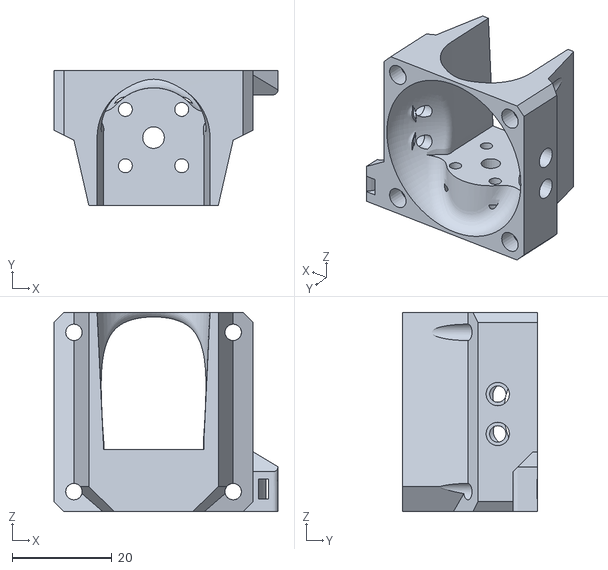
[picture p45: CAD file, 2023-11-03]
STL/hotend/hotend_rapido_uhf.stl
45.0 x 27.1 x 40.0

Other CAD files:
CAD/Test Assembly - Dragon BMO and BMG.step
CAD/Test Assembly w PCB - Dragon BMO and BMG.step
STL/misc/taller_x_axis_stop_block.stl
STL/pcb/mounts/pcb36_mount.stl
CAD/abl/abl_8mm_probe.step
CAD/abl/abl_bl_touch.step
CAD/abl/abl_cr_touch.step
CAD/abl/abl_cr_touch_uhf.step
CAD/bottom/klicky_bottom.step
CAD/bottom/kraken_klicky.step
CAD/bottom/kraken_stock.step
CAD/bottom/kraken_uhf_beacon.step
CAD/bottom/kraken_uhf_klicky.step
CAD/bottom/kraken_uhf_stock.step
CAD/bottom/stock_bottom.step
CAD/bottom/stock_bottom_uhf.step
CAD/drive/drive_bmg.step
CAD/drive/drive_lgx.step
CAD/drive/drive_lgx_lite.step
CAD/front/front_basic.step
CAD/front/front_fysetc_pis.step
CAD/hotend/hotend_dragon_bmo.step
CAD/hotend/hotend_mosquito.step
CAD/hotend/hotend_revo_micro.step
CAD/hotend/hotend_revo_voron.step
CAD/hotend/hotend_template.step
CAD/hotend/hotend_trianglelab_td6s.step
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

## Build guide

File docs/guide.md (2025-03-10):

---
title: Getting Started
summary: Introduction to E34M1 and this documentation
authors: Jon Harper
date: 2023-1-27
---

{% import 'badges.md' as badges with context %}

This page covers general topics about E34M1 and this documentation site.

!!! note
    E34M1 is *not* compatible with Mercury One Classic.

!!! tip
    Making a mod? Want to see how it looks in CAD? See the [`/CAD`][folder_cad] folder for a `STEP` files.

## Reading the Documentation

We use icons to condense and abbreviate these docs; these conventions are explained below.

### Icons and Terminology

| Icon/Term | Explanation |
|---|---|
| :material-printer-3d-nozzle: | Emphasizes that a part is 3D printed. |
| :material-cart: | Used for example links. *There are no affiliate links on this site.* |
| Drive module | Refers to the extruder, stepper, and mount for both. |
| FHCS | Flat head cap screw (DIN 7991) |
| SHCS | Socket head scap screw (DIN 912) |
| Voron inserts | M3 x 5mm OD x 4mm L heat set inserts, used by Mercury One.1 and E34M1. |
| EVA-style inserts | M3 x 4.6mm OD x 4mm L heat set inserts, mostly used by EVA and RatRig. |

### Tips

The [Modules](modules/index.md) section contains entries for every component and variant in E34M1. These
are labeled with *badges*, like so:

{{ badges.author('jonspaceharper', 'https://jon-harper.github.io') }}{{ badges.hsi() }}

These badges are meant to speed up reading through many entries at once. 

Tap or hover over the icon for an explanation of what each badges means. Some badges use text to provide
additional information, such as an contributor's name and profile link.

### PTFE Values

{{ badges.ptfe(22.5) }}

Hotends and drives (extruders) have a PTFE length value, indicated with a badge
like the one above. Add the two values to determine how much PTFE tubing you need between your hotend
and extruder.

### ABL Offsets

{{ badges.x_offset(8) }}{{ badges.y_offset(-15) }}

These badges are references for setting your ABL-to-nozzle offset in firmware. No badge
represents an offset of 0.

## Compatibility 

### Mercury One.1

E34M1 is compatible with Mercury One.1; in most configurations, no print area is lost by converting to EVA 3 from a different toolhead. In some configurations, adjustments are necessary to the Z axis (see the [Mercury One.1 Build Manual](https://docs.zerog.one/manual/build/mercury_eva/build_instruction) for details).

The chart below demonstrates build area for different Mercury One.1 builds.

| Base Printer/Rails | X Axis | Y Axis |
|---|---|---|
| Ender 5 Pro, 330mm rails | >= 265mm | >= 250mm |
| Ender 5 Plus | > 370mm | > 377mm |

{{ badges.length('Standard') }}

A few components are only compatible in specific combinations. This generally relates to whether a part is for a standard-length or UHF-length hotend.

The Hotend Length badge identifies if a component or variant is affected by hotend length.

### ABL

The chart below shows which ABL methods are supported by E34M1. Note that the side ABL mount is than EVA 3 stock and that not all ABL methods use them.

| | Standard Hotends | UHF Hotends | Mount Point |
|---|:---:|:---:|:---:|
| 8mm Probes | :white_check_mark: | :white_check_mark: | ABL |
| 12mm Probes | :x: | :x: | ABL |
| Beacon | :white_check_mark: | :white_check_mark: | Bottom/Rear |
| BL-Touch | :white_check_mark: | :white_check_mark: | ABL |
| CR-Touch | :white_check_mark: | :white_check_mark: | ABL |
| Klicky | :white_check_mark: | :white_check_mark: | Bottom |
| Klicky PCB | :x: | :x: | ABL |

### Bottom Horns

Most hotends are paired with Standard-length horns; longer hotends require the UHF bottom horns. The Mosquito has the Trihorns as a cooling workaround. Which see the [Hotend Modules](modules/hotend.md) for which bottom horns work with your hotend.

More about Bottom Horns can be found on the [Bottom Horns Modules](modules/bottom.md) page.

### Cable Management

There are two methods of cable management. The default attachment is the [Top](modules/top.md) module for umbilical users. Third parties offer PCB mounts supporting both umbilical (cable guide) and drag chains.

## Frequently Asked Questions

### How does this fit together?

Visit the [Tour](tour.md) to get an overview of how the modules are arranged. The [Assembly Guide](assembly/index.md) includes videos to assist during your build process.

### Is E34M1 supported by ZeroG or EVA?

No, this is a third-party project by [jonspaceharper](https://jon-harper.github.io) with community additions.

### What do I print?

See the Assembly guide's [Print Checklist](assembly/index.md#print-checklist) to ensure you have everything.

### What print settings should I use?

E34M1 follows the [ZeroG Print Settings](https://docs.zerog.one/standard/print/settings) guidelines.

All STL files are exported in print orientation.

### How are Voron-style and EVA-style inserts different?

Voron-style inserts are slightly thicker than EVA inserts. Mercury One relies on Voron-style inserts exclusively,
so all E34M1 components use them, as well. Third-party and stock EVA components use EVA-style inserts instead.

Does it matter? Yes: the adjustments we made for the larger, Voron-style inserts make insertion easier and parts
fit together better. Users report that it is generally still possible to use Voron-style inserts with parts made
for thinner inserts, but post-processing is needed.

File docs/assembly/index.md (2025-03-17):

---
title: Assembly Overview
summary: Introduction to assembling E34M1.
authors: Jon Harper
date: 2023-4-8
---

This guide covers assembly of a basic E34M1 build with a Rapido hotend, Sherpa Mini extruder, and BLTouch probe.

You should have your Mercury One build's X axis extrusion and linear rail assembled before following this guide. It is recommended that you include routing and securing the belts as part of the E34M1 build process, and will be prompted to do so.

!!! note "Beacon and Cartographer Users"
    These ABL types are not directly covered in this guide. Install your Beacon or Cartographer Low Profile probes according to the
    developer's documentation before starting E34M1 assembly.

## :material-printer-3d-nozzle: Print Checklist

Before continuing, check that you have all the printed parts necessary.

| Module | Example Part | Revision | Qty |
|---|---|---|---|
| [Front](../modules/front.md) | FYSETC Portable Input Shaper Front| v0.5 | 1 |
| Front | Belt Grabbers | v0.5 | 2 |
| [Top](../modules/top.md) | Left-Handed Top with Cable Guide  | v0.5 | 1 |
| [Bottom Horns](../modules/bottom.md)  | Dual Horns | v0.3 | 1 |
| [Rear Inlet](../modules/rear.md) | Single 5015 Fan | v0.2 | 1 |
| [Hotend Mount](../modules/hotend.md)  | Dragon BMO Mount | n/a | 1 |
| [Drive Mount](../modules/drive.md) | Sherpa Mini Drive Mount | n/a | 1 |
| [ABL Mount](../modules/abl.md) | BLTouch Mount | v0.3 | 1 |
| [Other](../modules/other.md) | Cable Guide | n/a | 1 |

Not all parts for E34M1 are covered in this guide. Other parts you may need or want for your build:

| Part | Purpose |
|---|---|
| [X Axis Stop Block](../modules/stop_block.md) | Adjustable bumper for the X axis limit switch. |
| [Z Endstop Mount](../modules/other.md#z-endstop-mount) | For Ender 5 Pros with stock Z axis; raises the Z limit switch. |
| [PCB Mount](../modules/pcb_mounts.md#pcb-mounts) | Mounts for toolhead PCBs. |
| [PCB Shrouds](../modules/pcb_mounts.md#pcb-shrouds) | Covers toolhead PCB wiring. |
| Rear Cable Arm | Raises and supports cable umbilical. |

## Considerations

### Time

Assembly time depends on your experience level and build configuration. Wiring and connecting the belts are not part of this guide, but some guidence is given on these topics.

Excluding wiring and belt routing, assembly time is approximately 30-45 minutes.

### Heat Set Inserts

All heat set inserts should be installed before beginning this guide. The [Modules & BOM](../modules/index.md) section includes locations for every heat set insert included with E34M1.

!!! warning "Warning: Heat Set Inserts"
    Stock EVA 3 uses M3 x 4.6mm OD x 4mm L heat set inserts. E34M1 maintains consistency with ZeroG and uses M3 x 5mm OD x 4mm L inserts (often called "Voron inserts"). Double-check which insert you should be using for third-party components to avoid damaging or ruining a printed part.

### Lock Washers

M3 lock washers are used extensively in this guide. Lock washers are not required but are strongly recommended to prevent loosening screws.

To emphasize that they are optional, lock washers are *italicized* in the guide's Parts lists.

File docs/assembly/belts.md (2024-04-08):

---
title: 4. Belts
summary: Finish out the Core components.
authors: Jon Harper
date: 2023-4-8
---

## Overview

<video controls="">
  <source src="https://jon-harper.github.io/E34M1/assets/vid/belts.mp4" type="video/mp4">
</video>

Now we can secure the belts. Note that if the belts are removed later, the hotend mount must be removed to re-install the belts.

!!! note "Note: Belt Lengths"
    Best practice is to have the same amount of belt under tension for top and bottom belts. To do this:

    1. The belts should be cut to the same length.
    2. The ends of the upper and lower belt should be even on both sides of the toolhead.

## Parts

| Part | Qty |
|---|---|
| :material-printer-3d-nozzle: [Belt Grabber](../modules/front.md) | 2 |
| 6mm GT2 belts | 2 |
| M3 x 6mm SHCS | 4 |
| *Lock washer, M3* | *4* |

## Steps

1. Locate the upper right belt catch on the Front module.
2. Take the end of a length of belt and face the ribs away from the X axis extrusion (towards the front of the printer). 
3. Slide 25-50cm (1-2") of the belt end through the *rear* hole for the belt catch.
4. Take the end of belt loop and fold it forward, then slip it out through the *forward* hole for the belt.
5. Draw some extra slack on the belt to keep it from slipping out easily; 10mm or more is plenty.
6. Using the second belt, repeat steps 1-4 with the lower belt catch. Leave *the same amount of excess belt*; the ends should be even.
7. Loop the end of both belts back on themselves so that the teeth face one another.
8. Press a belt grabber over the belts with the toothed side facing the belt.
9. Secure the belt grabber with two (2) M3 x 6mm screws and (optionally) lock washers.
10. Thread the two belts through the CoreXY system of your Mercury One build.
11. Check that each belt is seated on each idler and engages properly with the stepper's pulley.
12. Repeat steps 1-6 with with the left side of the toolhead.
13. Draw firmly and equally on both belts, then push the remaining belt grabber down to keep them from slipping.
14. Keep firm tension on the belt grabber and install the remaining two (2) 6mm screws with lock washers.

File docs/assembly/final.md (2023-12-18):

---
title: 8. Wiring and Final Notes
summary: Notes on wiring and finishing up.
authors: Jon Harper
date: 2023-4-8
---

## X Endstop Wiring

<figure markdown>
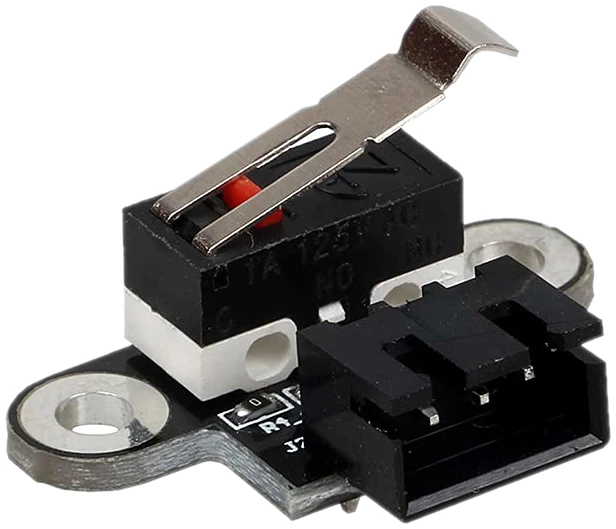
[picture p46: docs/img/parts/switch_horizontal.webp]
Horizontal limit switch

<figcaption>
Example of a mechanical limit switch from the BOM.
</figcaption>
</figure>

### Overview

Mechanical limit switch PCBs (as above) have a 3-pin JST-XH connector with the following pins:

1. Common (C)
2. Normally Open (NO)
3. Normally Closed (NC).

MCU endstop wire order example

MCU boards *also* have a 3-pin JST-XH connector for endstops, but they are typically wired as seen in the graphic at right:

1. +5V
2. GND
3. SIG (pin 1.29 in the illustration)

### Wiring the Endstop

Although both sides have a 3-pin connector, the endstop connection only needs two (2) wires. Unfortunately, limit switch PCBs are often sold with a *3-wire* cable. This is hazardous if the +5V pin is connected to the endstop, and may start a fire.

!!! warning
    Never connect a +5V pin to a mechanical endstop.

These are the correct pins to connect:

| Pin | Switch Pin | Board Pin |
|---|---|---|
| 1 | C (to SIG) |*(Unused)* | 
| 2 | *(Unused)* | SIG |
| 3 | NC (to GND) | GND |

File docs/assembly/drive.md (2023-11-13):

---
title: 6. Drive Module
summary: Assembling the extruder and stepper.
authors: Jon Harper
date: 2023-4-8
---

## Overview

<video controls="">
  <source src="https://jon-harper.github.io/E34M1/assets/vid/drive.mp4" type="video/mp4">
</video>

The final major remaining piece of assembly is the extruder and stepper motor. If you are using a PCB mount, prefer to install the mount before proceeding (if possible).

## Parts

!!! note
    There are eight (8) screw holes to attach the Drive module, but not all will be used. The Drive attaches to the Front module with 8mm screws; use 12mm screws for the Top module.

Drive designs not from E34M1 are compatible but do not leave room for lock washers. They should be left out if you are using a third party or stock EVA 3 drive mount.

| Part | Qty |
|---|---|
| :material-printer-3d-nozzle: [Drive mount](../modules/drive.md) | 1 |
| Assembled Sherpa Mini extruder and stepper | 1 |
| PTFE tube, approx. 45.8mm | 1 |
| M3 x 12mm SHCS | 2 |
| M3 x 8mm SHCS  | 6 |
| M3 x 6mm BHCS | 1 |
| *Lock washers, M3* | *9* |

## Steps

1. Set the printed Drive module over the Front and Top. The hexagonal hole is for the PTFE tube; this can be used to orient the part.
2. Use four (4) M3 x 8mm screws with lock washers to attach the Drive to the Front module.
3. Use two (2) M3 x 12mm screws with lock washers to attach the Drive to the Top module.
4. Insert the PTFE tube through the hexagonal cutout and into the Hotend module. It may be a tight fit; some users recommend rounding the cutout with a precision hobby knife.
5. Place the assembled Sherpa Mini extruder in place. There is a rounded ledge to support the stepper.
6. Secure the extruder to the top of the mount with two (2) M3 x 8mm screws with lock washers.
7. Finally, secure the front of the extruder with a single M3 x 6mm BHCS. Alternatively, use a zip tie around the stepper motor.

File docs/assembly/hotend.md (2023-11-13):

---
title: 5. Hotend Module
summary: Assemble and install the hotend module.
authors: Jon Harper
date: 2023-4-8
---

## Overview

<video controls="">
  <source src="https://jon-harper.github.io/E34M1/assets/vid/hotend.mp4" type="video/mp4">
</video>

We're ready to install the hotend. The hotend, fan, thermistor, and heater cartridge are all meant to be removable as once piece, so we assemble them first.

## Parts

| Part | Qty |
|---|---|
| :material-printer-3d-nozzle: [Hotend Module](../modules/hotend.md) | 1 |
| Phaetus Rapido Hotend | 1 |
| 40mm x 10mm axial fan | 1 |
| M2.5 x 8mm SHCS | 4 |
| M3 x 6mm SHCS | 4 |
| M3 x 12mm SHCS | 4 |
| *Lock washer, M3* | 4 |

## Steps

!!! tip "Tip: Fan Direction"
    The 40mm fan should blow *towards* the hotend. A fan's airflow direction is usually the side with the manufacturer's sticker on it.

1. Align the hotend's mounting holes with the Hotend module. Hotends with asymmetric heater blocks like the Dragon should have the longer/larger side facing *forward*.
2. Secure the hotend with four (4) M2.5 screws.
3. Install the hotend's heater cartridge and thermistor.
4. Place the 40mm fan on the hotend mount with the airflow directed *towards* the hotend. Rotate the fan so that the wiring trails to the top right edge.
5. Use four (4) M3 x 12mm screws to install the fan. 
6. Use a zip tie to secure the fan, heater cartridge, and thermistor to the zip tie anchor at top right.
7. Place the hotend assembly into the EVA 3 Front.
8. Secure with four (4) M3 x 6mm screws and lock washers.

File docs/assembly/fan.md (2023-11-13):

---
title: 3. Part Cooling Fan
summary: Finish out the Core components.
authors: Jon Harper
date: 2023-4-8
---

## Overview

<video controls="">
  <source src="https://jon-harper.github.io/E34M1/assets/vid/pcf.mp4" type="video/mp4">
</video>

## Parts

| Part | Qty |
|---|---|
| 50mm x 15mm radial fan | 1 |
| M3 x 20mm SHCS | 1 |
| *M3 washer* | 1 |

## Steps

1. Place the fan exhaust into the rear inlet. The fan's screw hole should line up with the rear heat set insert.
2. Secure the fan with the M3 x 20 screw. Optionally, add an M3 washer first to prevent cracking the fan from overtightening.

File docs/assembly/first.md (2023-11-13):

---
title: 1. First Steps
summary: Assembling the Top, endstop, and cable guide.
authors: Jon Harper
date: 2023-4-8
---

## Overview

<video controls="">
  <source src="https://jon-harper.github.io/E34M1/assets/vid/top.mp4" type="video/mp4">
</video>

First, we assemble the Top, including X axis endstop and cable guide/wire anchor.

## Parts

| Part | Qty |
|---|---|
| :material-printer-3d-nozzle: [Printed Top](../modules/top.md) | 1 |
| :material-printer-3d-nozzle: [Cable Anchor](../modules/top.md) | 1 |
| :material-printer-3d-nozzle: [Cable Guide](../modules/top.md) | 1 |
| MGN12H carriage (X axis) | 1 |
| Horizontal limit switch | 1 |
| M3 x 8mm SHCS | 4 |
| M3 x 6m SHCS | 5 |
| *Lock washer, M3* | *5* |

## Steps

!!! note
    If you printed a right-handed Top, reverse left and right in the directions below.

1. The cable anchor attaches to the rear left of the Top with a lock washer and an M3 x 6mm screw. Orient the two inserts on the anchor to the rear or left side of the Top. 
2. Secure the cable guide to the cable anchor with two (2) M3 x 6mm screws.
3. Align the endstop with the connector oriented upwards. Secure with two (2) M3 x 6mm screws.
4. Set the assembled Top on the X axis MGN12H carriage. The wire cutout and cable anchor should be towards the rear of the printer.
5. Attach the Top with four (4) lock washers and M3 x 8mm screws.

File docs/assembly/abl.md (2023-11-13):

---
title: 7. ABL Side Mount
summary: ABL installation and final notes.
authors: Jon Harper
date: 2023-4-8
---

## Overview

<video controls="">
  <source src="https://jon-harper.github.io/E34M1/assets/vid/abl.mp4" type="video/mp4">
</video>

This is the last step in this guide. After this, all that remains is finishing out wiring.

## Parts

| Part | Qty |
|---|---|
| :material-printer-3d-nozzle: [BLTouch mount](../modules/abl.md) | 1 |
| BLTouch | 1 |
| M3 x 6mm SHCS | 4 |

## Steps

1. Secure the BLTouch to the mount with two (2) 6mm screws.
2. Attach the mount to the EVA 3 toolhead with two (2) 6mm screws in the mount arm.

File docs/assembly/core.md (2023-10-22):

---
title: 2. Core Assembly
summary: Combining the Core parts of EVA 3.
authors: Jon Harper
date: 2023-4-8
---

## Overview

<video controls="">
  <source src="https://jon-harper.github.io/E34M1/assets/vid/core.mp4" type="video/mp4">
</video>

With the Top installed, we next build the rest of the Core using the Front, Bottom, and Rear modules.

!!! note "Note: Bottom-mounted ABL"
    - Klicky: install the magnets and wiring to the Bottom beforehand.
    - Beacon: wiring should be done beforehand. If soldering your Beacon wires to the PCB, you will also need to install the Beacon.

## Parts

| Part | Qty |
|---|---|
| :material-printer-3d-nozzle: [Rear Inlet](../modules/rear.md) | 1 |
| :material-printer-3d-nozzle: [Bottom Horns](../modules/bottom.md) | 1 |
| :material-printer-3d-nozzle: [Front](../modules/front.md) | 1 |
| M3 x 45mm SHCS | 4 |
| M3 x 6mm SHCS  | 1 |
| *Lock washer, M3* | *5* |

## Steps

1. Use a single M3 x 6mm screw and lock washer to fasten the Bottom Horns and Rear Inlet together.
2. Put an M3 x 45mm screw and lock washer through each of the top two (2) screw holes on the Rear Inlet.
3. Slide the screws from front to back through the holes on the Top.
4. Take large, flat side of the Front and align the upper two (2) inserts with installed 45mm screws. Thread the screws in and tighten.
5. Slide the remaining two (2) M3 x 45mm screws with lock washers through the bottom holes in the Rear Inlet. Thread the screws into the back of the Front component and tighten.

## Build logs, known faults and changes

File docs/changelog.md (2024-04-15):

---
title: Changelog
summary: Log of changes to E34M1.
authors: Jon Harper
date: 2023-1-26
---

## April 2024

### 04/11

- Bottom: Beacon RevH support, Kraken tweaks

### 4/5

- Top: support for built-in microswitches

##  March 2024

### 3/18

- Drive: Orbiter 2 tweaks, updated to v3

### 3/11

- Top: Prettified integrated microswitch entries.
- Docs: Fixed some cosmetic issues.
- Docs: Merged in the latest backend version from OmniBox.

## February 2024

### 2/26

- Top v0.8: updated STEP files.

### 2/8

- Kraken v0.6: Updated STEP files.

### 2/7 

- Kraken v0.6: Tweaked mounting holes.

## January 2024

### 1/28

- Added new 8mm probe mounts for regular and UHF.

### 1/27

- Thickened insert walls for the Owl Eyes rear intake.
- Added Beacon support to Owl Eyes.

### 1/16

- Updated STEP master file.

### 1/5

- Added Kraken STEP files.

## December 2023

### 12/19

- Added HSI admonitions.
- Finished integrating automated pages.

### 12/16-18/23.

- Working towards integrating automation.
- Added numerous missing parts:
    - Creality Sprite SE entry
    - Galileo SA
    - Mellow NF-Crazy
- Added a lot of typos.
- Updated a bunch of entries.
- Top: Added v0.8, which centers to the Top piece on the MGN12H carriage.

### 12/13/23

- Merged in Creality Sprite SE drive.

### 12/10/23

- Added Galileo 2 SA (thanks cuiviemen)
- Added Papst RL35-8 fan rear inlets (thanks again, cuiviemen)

### 12/4/23

- Fixed videos

## November 2023

### 11/27/23

- Added numerous third-party modules.
- Added cuiviemen's Papst RLF35-8 intake.
- Added dual 5015 (Owl Eyes) rear inlet.

### 11/13/23

- Updated assembly steps to R2.
- Numerous fixes and edits for R2 all over the site.
- Integrated third party hotends and extruders into the modules section; removed compatibility pages completely.
- Moved Tour Guide to top level.
- Updated assembly part list to R2.

### 11/12/23

- Reworded some of the guide introduction.
- Cleaned up the end of the Tour.

### 11/3/23

- Hotends, Tour, Front, ABL: fixed numerous errors and updated illustrations
- Compatibility page: updated tables
- Bottom Horns: moved Beacon UHF up 0.6mm; lightened part

### 11/2/23

- Rear Inlet: added Beacon versions of new sideways 5015 and CPAP inlets.
- Rear Inlet: cleaned up airflow path inside new inlets.
- Bottom: Fixed print orientation on two files.
- Top: updated page to R2
- Rear: updated page to R2

## October 2023

### 10/30/23

- Rear Inlet: new template for making inlets, part of Release 2.
- Rear Inlet: updated sideways rear inlet and 15mm CPAP rear inlet to new template, part of Release 2.

### 10/29/23

- Fixed a number of links.
- Migrated multiple files from `testing` to `main`.
- Initial Release 2 commit to `testing` branch.
- ABL: cleaned up page somewhat
- Toolhead PCBs: added deprecation note

### 10/21/23

- Top: added a sensorless homing top
- Assembly: corrected that M3 x 45mm screws are used for the Rear Inlet.
- Assembly: clarified how to attach the Drive module.

### 10/20/23

- Rear Inlet: fixed inlet link

## September 2023

### 23/09/30

- Assembly: Fixed a dead link. Thanks to [dhazelett](https://github.com/dhazelett) for the edit.
- Assembly: Fixed some stale info.

### 23/09/27

- Added new Dragon UHF mount to `testing`.
- Added Dragon UHF mount to docs.

### 23/09/11

- Cleaned up `testing` branch, removed stale files.
- Bottom Horns: even lighter stock dual horns
- Bottom Horns: added UHF stock horns
- Updated compatibility charts.
- Top: updated docs to v0.5

### 23/09/04

- Bottom Horns: updated Klicky entries and a added a missing Beacon link
- Bottom Horns: added lighter v0.2 for stock and Beacon dual horns

### 23/09/03

- Drives: Updated and fixed Annex Sherpa Mini docs.

## July 2023

### 23/07/13

- Updating docs to fix stuff that's been missing lately.
- Drives: Commited Sherpa Mini mount for testing and added to docs.

### 23/07/09

- Rear: Added 15mm CPAP
- Bottom: Added Klicky UHF
- Began work on Sherpa Mini support.

## June 2023

### 23/06/08

- Front 0.4: *very* slightly tweaked belts and a better portable shaper front (can be mounted without removing the fan)
- Updated all STEP files
- Cleaned out stale files from the `testing` branch.

## May 2023

### 23/05/16

- Shrouds: added to testing version with a wider "mouth" for the umbilical.
- Shrouds: fixed print orientation.

### 23/05/13

- Front: fix for Portable Input Shaper, now v0.3

### 23/05/08

- Added Y offset info for Klicky.

### 23/05/06

- Cleanup and finishing up the Guide section.
- Added to the FAQ.
- Stop Block: added E5Plus stop block.
- Added final section to Assembly for notes.

### 23/05/05

- Began reorganizing documentation in Guide, Reference, and Assembly

### 23/05/04

- Added a section in Compatibility about filament sensors.
- Sections in the navigation pane now auto-expand.

### 23/05/03

- Top: Added left-handed version of the Top module (endstop on the left side).
- Top: updated documentation with changes from yesterday and today.
- Stop Block: added separate page for X axis stop blocks.
- Stop Block: added Max X stop block.

### 23/05/02

- Top: X endstop now mounts with heat set inserts.
- Top: Improved free overhangs for insert holes.

## April 2023

### 23/04/27

- Docs: All modules now have revision information.
- Front: merged in v0.2 that fixes the belt angle issue.

### 23/04/27

- ABL: BLTouch from scratch.

### 23/04/26

- Assembly: updated belts video to include inserting the belts

### 23/04/25

- ABL: moved CR Touch out 1mm.
- Front: more test iterations.
- Started work on a version history page.
- ABL: added new BLTouch mount.
- Rear Inlets: added a Dual 5015 modified from stock.
- Drives: added `drive_bmg.stl` and `drive_lgx_lite.stl` to the main branch.

### 23/04/24

- Front: made several iterations of a belt angle fix.
- Front: new belt catches with better engagement.

### 23/04/20

- Added drive module images.
- Finished drive module docs.
- Tweaked Modules navigation layout.
- Added missing ABL messages.
- Uniform BOM part names.

### 23/04/19

- Combined PCB shrouds and mounts to one page.
- Tons of editing for wording and clarity.
- Added new drive modules to `testing`. See Below.
- All:
    - Modified for Voron inserts, where applicable.
    - Made room for lock washers on all fasteners.
- BMG:
    - Added bottom chamfer.
    - Cosmetic changes.
- LGX:
    - Mount is slightly lighter.
    - Reinforced extruder mounting arms.
- LGX Lite:
    - Mount is lighter.
    - Fixed overhangs for mounting screws.
    - Added bottom chamfer.
- Orbiter 1.5:
    - Mount is slightly lighter.
- Orbiter 2.0: 
    - Mount is slightly lighter.
    - Added bottom chamfer.

### 23/04/18

- Lots of formatting and cleanup.
- Assembly: added note about other parts to consider (including X limit switch bumper)
- Added CR Touch back in.
- **GitHub**: All parts now have part numbers printed on.
- **GitHub**: All parts are now in print orientation.
- All assembly pages are now numbered.

### 23/04/14 - 23/04/15

- Worked on hotends and extruders.

### 23/04/13

- Began altering hotends and drives for Voron inserts.
- Lots of minor doc edits.
- Created the `testing` branch for parts not yet ready.
- Started opening issues on the GitHub repository.

### 23/04/12

- Added E3D V6 and Revo V6 to the hotends page.
- Lots of minor edits.
- Reformatted the modules pages, added a description.

### 23/04/11

- Optimized the design of the sideways inlet.
- Worked with cuiviemen on an improved Beacon inlet and bottom.

### 23/04/09

- Finished assembly docs.
- Added notes to several modules.
- Updated git license to reflect EVA 3 license (CC BY-NC-SA 4.0).
- Downconverted video and delayed download.

### 23/04/08 

- Added assembly docs outline.

### 23/04/07

- Added license and credits.
- Added images to hotends and extruders pages.
- More formatting to the landing page.

### 23/04/06

- Updated graphics and added missing graphics.
- Finished inlining BOM and insert data.
- Added accreditation to parts that are mods (mostly bottom horns)
- Updated landing page.
- Expanded compatibility page with known hotends and drives.

### 23/04/05

- Visual refresh:
    - BOM and heat set insert pages are combined into a Modules category.
    - TOC is integrated into the left along with each section.
- Updated docs with Trihorn and Klicky Trihorn.
- Updated doc links.
- Renamed a number of files.

### 23/04/04

- Added Trihorn and Klicky Trihorn
- Began prepping STLs and CAD to move to the E34M1 repo.

## March 2023

### 23/03/30

- Added CR Touch and CR Touch Volcano entries.
- Cleaned up some wording in the docs.

### 23/03/28

- Cut down significantly on duplicate documentation.

### 23/03/27

- Added the Tour page.
- Significant rework of other sections began.

### 23/03/24

- Added several mods.
- Slightly clarified the compatibility page about PCB mounts.

### 23/03/23

- All PCB mounts: strengthened middle criss-cross for less flex.
- All PCB mounts: added 1mm clearance between PCB and screws behind.
- `pcb36_mount_cable_chain.stl`, `pcb42_mount_cable_chain.stl`: Moved mount for chain further to the edge.

### 23/03/20

- `pcb36_mount_cable_chain.stl`, `pcb42_mount_cable_chain.stl`: New PCB mounts that support 10x11 open cable chain.
- Lots of documentation edits and updates.

### 23/03/18

- `pcb_shroud_30mm_fan.stl`: added a new shroud that mounts a 30mm fan for CANBUS users.

### 23/03/11

- `top_endstop_mgn12h.stl` & `top_endstop_mgn12h_pcb.stl`: moved modifications from `/testing` folder.

### 23/03/10

- `belt_grabber.stl` Smaller to match changes to the front piece.
- `front_universal_fi.stl`, `front_universal_pis_fi.stl`: Narrowed belt loops and inserts for mounting belt catches.
- The above have been fit tested and aare committed.
- `top_endstop_mgn12h.stl`: significantly strengthented the cable guide mount.
- `top_endstop_mgn12h_pcb.stl`: cosmetic modifications.

## February 2023

### 23/02/01

- `bottom_horns_klicky_fi.stl`: Modified Klicky horns (still in testing!)
- `5015_sideways_inlet.stl`: Thickened hex grill; it broke off on the build plate. >:(
- Merged contents of `EVA3` branch into `main`. This should help avoid confusion to newcomers to the repo.
- Added EVA34M1 on Printables.
- `bl_touch_volcano_mount.stl`: New ABL mount for Volcano hotends.

## January 2023

### 23/01/26

- Deployed new doc site.
- Updated STEP files.

### 23/01/24

- `front_universal_pis_fi.stl`: Added FYSETC PIS (portable input shaper) support
- `pcb36_mount.stl`, `pcb42_mount.stl`: Added two files for, e.g., EBB36 and EBB42 stepper-mounted PCBS.
- These should support *all* stepper mounted PCBs, not just CANBUS (e.g., BTT Piggyback36).
- `pcb_shroud.stl`, `pcb_shroud_cat.stl` two shrouds to cover up the PCB wiring added (one is whimsical).

### 23/01/23

- Alternate top piece removes the cable support mount entirely now.
- Started work on rear PCB mount with integrated cable support instead.

### 23/01/20

- `bltouch_mount.stl`: Strengthened BLTouch bracket.

### 23/01/19

- Fixed missing screw holes in the alternate top piece.
- Shortened the front intake duct by 1mm.
- Updated all outdated STEP files.

### 23/01/18

- `5015_sidways_inlet_fi.stl`: Added some walls for the 5015 fan to sit in and a notch for the bit around the exhaust.
- Added a Z limit switch mount to raise the limit switch height. Comes with a cover.
- Added a front intake duct that lets you remove the fan with two screws instead of four.
- Note: the intake duct is not compatible with 4020 fans (or you lose Y space).

### 23/01/16

- Belt fit test is good.
- Added a bumper for the X axis limit switch.

### 23/01/13

- Fit test appears ready for testing on a working Merc.
- Added cutout in belt grabber for divider between belts.
- Added a version of the cable guide post with the guide to the side.

### 23/01/12

- Tweaked post again for cable guide.
- Spent most of the day fixing a printer.

### 23/01/11

- Tagged all parts in the Fusion model with part numbers to scrape BOM data.
- Tweaked BLTouch mount to add a little more material.
- Added a readme with BOM info.
- Added a chamfer to the top piece insert holes and an overhang for the endstop mount.
- Test fitting went well:
    - Found & fixed missing BLTouch holes in the front piece.
    - Made cable guide tower thinner to avoid blocking drive piece.
    - Rotated cable guide around to face completely backwards.
- Added CAD files for Volcano duct.
    - The duct source file has broken geometry that I am unable to fix.
    - I have made the changes otherwise needed to make the duct compatible.

### 23/01/10

- Started changelog
- Switched M3 inserts to Mercury One-style to simplify BOM.
    - All parts now use M3x5x4mm inserts.
    - Added Dragon BMO part with resized insert holes.
- Refactored Fusion 360 files;
    - Split out small Core parts into individual files
    - Removed a lot of quick hacks
- Added divider to belt grabber between belts.
- Re-oriented parts to export in the correct orientation for print.
- Endstop is now EVA-style horizontal and mounted on the right.
    - Ditched rear-mounted endstop design.
    - Still need to design a bumper for the endstop.
- Cable guide improvements:
    - Rotated guide mount 45 degrees to stay out of the way of endstop.
    - Closer to rear toolhead and takes less X axis space.
    - Raised cable guide 15mm.
    - Rear of cable guide allows for larger zip ties.
- BLTouch mount:
    - Moved mount points over belt clamp
    - Design a new BLTouch mount
    - Uses a simple cutaway support structure

### 23/01/07

- Started work

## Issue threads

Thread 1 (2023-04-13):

CR Touch support

jon-harper, 2023-04-13:
Pending fit testing. **ON HOLD** for redesign.

## CR Touch BOM

| Part | Qty |
|---|---|
| [cr_touch_mount.stl](https://github.com/jon-harper/E34M1/blob/testing/STL/abl/cr_touch_mount.stl) | 1 |
| Heat Set Insert, M3x5x4 | 2 |
| M3 x 6mm SHCS | 4 |

jon-harper, 2023-04-23:
Discord report that this touches the horns. I'll move it out 1mm.

jon-harper, 2023-04-25:
New revision up.

InfinitiVoid, 2023-09-13:
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
The new revision of CRTouch fits, works as intended.

X-offset: 41mm
Y-offset: 2mm

(offsets works for me, probably needs indepth calibration but I am too stupid for that)

jon-harper, 2023-09-13:
I appreciate it. I haven't closed this--but forgot to notate--that the mounting arm slightly angles the CR Touch towards the nozzle. I think this is an artifact of ABS shrinkage, but have not yet resolved it.

InfinitiVoid, 2023-09-14:
Yea, I noticed, this is the second one I printed. ASA with a 10mm brim and good supports works fine for me

jon-harper, 2023-11-17:
Closing this, as there is a new CR Touch mount with Release 2.

Closed 2023-11-17.

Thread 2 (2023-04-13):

Improved Beacon horns and trihorns

jon-harper, 2023-04-13:
There are three new Beacon mounts, courtesy Cuiviemen. These all allow the connector to remain on the Beacon. They require a Rear Inlet that's also in the `unstable` branch.

## Rear Inlet BOM

| Parts | Qty |
|-------|-----|
| [rear_inlet_beacon.stl](https://github.com/jon-harper/E34M1/blob/testing/STL/rear/rear_inlet_beacon.stl) | 1 |
| Screw, M3-0.5 x 6mm FHCS | 1 |
| Screw, M3-0.5 x 20mm     | 1 |
| Screw, M3-0.5 x 45mm      | 4 |
| Heat Set Insert, M3x5x4   | 1 |
| 5015 Radial Fan           | 1 |

Note that the M3 x6 is a flat head cap screw.

## Dual Horns BOM

| Parts | Qty |
|---|---|
| [beacon_bottom.stl](https://github.com/jon-harper/E34M1/blob/testing/STL/bottom/beacon_bottom.stl) | 1 |
| Heat Set Insert, M3x5x4   | 3 |
| Low-Profile Beacon Kit    | 1 |

## Trihorn BOM

| Parts | Qty |
|---|---|
| [beacon_bottom_trihorns.stl](https://github.com/jon-harper/E34M1/blob/testing/STL/bottom/beacon_bottom_trihorns.stl) | 1 |
| Heat Set Insert, M3x5x4   | 3 |
| Low-Profile Beacon Kit    | 1 |

## Dual Horns No HSI BOM

This uses bare screws to attach the Beacon mount and may have slightly improved airflow.

| Parts | Qty |
|---|---|
| [beacon_bottom.stl](https://github.com/jon-harper/E34M1/blob/testing/STL/bottom/beacon_bottom.stl) | 1 |
| Heat Set Insert, M3x5x4   | 1 |
| Low-Profile Beacon Kit    | 1 |

jon-harper, 2023-04-20:
Docs updated yesterday.

Closed 2023-04-20.

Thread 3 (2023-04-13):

Not all STLs are in print orientation

jon-harper, 2023-04-13:
Call 'em as you find 'em so they can be fixed.

jon-harper, 2023-04-14:
- At least one Bottom (too tired to look now, but I think a Klicky)
- Dragon hotend mount

jon-harper, 2023-04-20:
Fixed yesterday.

Closed 2023-04-20.

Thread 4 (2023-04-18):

Add hardware links to BOM

jon-harper, 2023-04-18:
X endstop can be hard to source or confusing. It'd be helpful to have links to other hardware, too.

jon-harper, 2023-04-20:
Added.

Closed 2023-04-20.

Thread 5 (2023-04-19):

Drive modules need BOM and fit testing

jon-harper, 2023-04-19:
There are drive modules in the `testing` branch that need fit testing. Please let me know here if you've tried one out.

Drives remaining to test:

- LGX
- ~~Orbiter 1.5~~
- ~~BMG~~
- ~~Orbiter 2.0~~
- ~~LGX Lite~~

k-piekarczyk, 2023-04-19:
I can test the Orbiter 2.0 one next week when I have some more free time.

jon-harper, 2023-04-20:
> I can test the Orbiter 2.0 one next week when I have some more free time.

Awesome, thank you!

ratheon2474, 2023-04-25:
I can confirm the LGX Lite mount works

k-piekarczyk, 2023-04-26:
The Orbiter 2.0 seems to be working fine as well 😄

Closed 2023-10-23.

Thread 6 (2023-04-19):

Belt holder a bit too high (Merc One.1, v1.1.3)

k-piekarczyk, 2023-04-19:
Hi @jon-harper!
First of all I love that you adapted EVA3 for Merc One.1, and the fact that you took your time to show some assembly instruction.

The belt grabbers seem to be 2-3 mm to high (at least for my setup), as pictured.

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

Would you be willing to share the STEP file for the front mount (the one with holes for ADXL345), so I can fix that for myself? I couldn't find it in the files already in the repo, but maybe I missed it.

jon-harper, 2023-04-20:
First, here's the latest [Core assembly STEP file](https://github.com/jon-harper/E34M1/blob/main/CAD/Core.step). For some reason it wasn't uploaded.

OTOH, you should not have have that angle on the belts. The only time I've seen this is with the early revision front before the belt catches had a divider. I can't see from this angle, but the belt catches should look like this:

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

If you have an older Front piece without the divider you can still straighten the belts; it just takes more fussing.

If none of that helps you, can you send pics of both sides of your belt catches?

k-piekarczyk, 2023-04-21:
From what I can see, the front I got from the documentation website (11.04.2023) is different, the new one should fix my issue, I'll find out diring the weekend :)

Disaster1971, 2023-04-23:
Same Issue I'm having with my belts. I think it might be effecting the bltouch mount to were the nozzle sitting higher then the bltouch

jon-harper, 2023-04-23:
At this point I'm considering this an open issue in need of a fix. I'm recovering today from traveling but plan to test a solution tomorrow.

jon-harper, 2023-04-26:
Two of us are now running the modified front from [this commit](https://github.com/jon-harper/E34M1/commit/b297bf8145c11a9171a5439548775daa3bd0f18a) and it looks good.

The belt catches dropped 1mm. Both experimentation and measurements keep coming up with *exactly* 1mm, so I'm suspecting I made a math error along the way in CAD.

Considering printing the new belt grabbers, as well. They do a better job engaging the belts without bowing.

k-piekarczyk, 2023-04-26:
The v0.1 version of the front works fine for me now, though I must admit that the new belt loop instead of the earlier open back design was inconvenient to mount, since the top of the belt loop drooped a bit, making it impossible to just push the belt through.

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

jon-harper, 2023-04-26:
> The v0.1 version of the front works fine for me now, though I must admit that the new belt loop instead of the earlier open back design was inconvenient to mount, since the top of the belt loop drooped a bit, making it impossible to just push the belt through.
>

I think you may have the wrong file. It sounds like you printed an older test version that I accidentally committed and later replaced. Not sure what happened, but the version I linked should be labeled v0.2. It's the latest `stock_front.stl` in the testing branch if you want to grab it from there.

jon-harper, 2023-05-02:
Several users are running v0.2 now and it's included merged into `main`. :+1:

Closed 2023-05-02.

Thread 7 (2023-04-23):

Dual 5015 Rear Intake Fit Testing

jon-harper, 2023-04-23:
There's a new, dual-5015 radial fan rear intake. It's modified from a stock EVA 3 "cooling inlet" to E34M1-style with screw holes for the 4x 45mm screws that hold the Core together.

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

## Bill of Materials

| Parts | Qty |
|---|---|
| [`dual_5015_inlet.stl`](https://github.com/jon-harper/E34M1/blob/testing/STL/rear/dual_5015_inlet.stl) | 1 |
| 5015 radial fan | 2 |
| M3 x 45 SHCS | 4 |
| M3 x 6mm SHCS | 1 |
| Lock washer, M3 | 5 |
| M3 x 20mm SHCS | 2 |
| Heat set inserts, M3x5x4 | 2 |

sylwester-, 2023-05-02:
printed it yesterday. fits well, works well!

jon-harper, 2023-05-02:
Thanks @sylwester- !

Closed 2023-05-02.

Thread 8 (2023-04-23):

40mm fan intake and rear intake adapter are not compatible.

jon-harper, 2023-04-23:
It's impossible to get the 25mm crossbar screw in along with the top left 45mm screw.

zephyr2206, 2024-04-29:
Still same issue. Could it be solved by just adding a few mm thickness to the adapter so the screws will clear each other?

jon-harper, 2024-04-29:
It might be fixable that way, but the 40mm fan is suboptimal in several ways. The Owl Eyes dual inlet and CPAP are better choices without adding a lot of weight and losing build space.

jon-harper, 2025-03-17:
Wontfix

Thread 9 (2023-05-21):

PIS will not mount with the hotend fan in place

jon-harper, 2023-05-21:
The portable input shaper could move up about 1-2mm and allow the sensor to be mounted without removing the fan.

jon-harper, 2023-06-28:
Fixed with version 0.3

Closed 2023-06-28.

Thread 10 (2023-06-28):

CPAP Support

jon-harper, 2023-06-28:
I have designed (and a user has tested) a 15mm CPAP rear part and am working on a 22mm part.

It still needs to be documented and the 22mm part tested.

jon-harper, 2023-11-17:
15mm is tested thoroughly. The 22mm part needs a redesign to the new template.

jon-harper, 2025-03-17:
A third party has created a mount for this: https://www.printables.com/model/1176116-e34m1-18mm-cpap-rear-inlet

Closed 2025-03-17.

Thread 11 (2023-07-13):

Sherpa Mini fit test

jon-harper, 2023-07-13:
Sherpa Mini has a mount available, but fit test is pending. See the docs.

sharpner, 2023-07-27:
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

I use that mount, the only thing that did not quite work was to get that screw in there - but it works okayish without :-)

jon-harper, 2023-07-27:
> 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
>
> I use that mount (https://github.com/jon-harper/E34M1/blob/testing/STL/drives/drive_sherpa_mini.stl), the only thing that did not quite work was to get that screw in there - but it works okayish without :-)

Was the screw hole off or is there not clearance with the ADXL?

sharpner, 2023-07-27:
There is no clearance (without the board of course) - I can remove my board and make a photo later to better show the problem

jon-harper, 2023-08-25:
> There is no clearance (without the board of course) - I can remove my board and make a photo later to better show the problem

Gotcha, I've got it installed now and see the issue. Did you try with a button head screw? I'm using the PIS front and it just fit.

sharpner, 2023-09-01:
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
Similar, but I just rasped it of a bit and now I got the screw in there 🤷‍♂️

jon-harper, 2023-09-01:
Do you happen to have a button head screw to test it with? It fits with a button head on mine but I'm using the PIS front.

sharpner, 2023-09-02:
ah sorry, I assumed you meant SHCS because I was using the button head screw initially. As you can see I used it for the other two screws as well. Yes I am using one now, but after I scraped off a bit.

jon-harper, 2023-09-04:
> ah sorry, I assumed you meant SHCS because I was using the button head screw initially. As you can see I used it for the other two screws as well. Yes I am using one now, but after I scraped off a bit.
>
> So it's no longer an issue for me if you want to close the ticket xD

I made a note about the clearance issue and recommended a button head screw there. I'll push the updated docs soon.

Thanks for your help!

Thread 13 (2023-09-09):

EBB42 does not fit

drright72, 2023-09-09:
EBB42 CANbus board does not fit when using dual 5015 fan inlet.

jon-harper, 2023-09-09:
This version is in testing to address that: https://github.com/jon-harper/E34M1/blob/testing/STL/rear/dual_5015_inlet.stl

A user gave a preliminary report that it fits, but hasn't been able to use it. Let me know how it goes so I can merge it into the `main` branch if it works or fix any issues if they occur.

Thanks!

drright72, 2023-09-09:
This barely accommodates the EBB42 board on a 23.5mm stepper, but WITHOUT the CAN board mount. I think making the base 10mm thicker would cover it.

jon-harper, 2023-09-10:
It didn't click that you are using a BMG. Most folks have or are moving away from NEMA17 because of size and weight; the BMG/NEMA17 is the largest drive module. The dual rear inlet is the largest rear module, as well, and has been redesigned twice to reduce the size and get it working with NEMA14-mounted PCBs. There's just very little room to adjust things in there.

My recommendation is to go single rear inlet until you can switch to a NEMA14 and Sherpa Mini (it's printed and uses BMG parts, so no need to buy the extruder). Another option would be a 10mm shim under the drive module that you mentioned, though that comes with its own issues.

drright72, 2023-09-10:
Yes, I'm using the BMG. I do have the parts for Sherpa, and had intended on using it with an EBB36. Unfortunately I decided on the Sherpa Micro before realizing there's no good way to secure the motor like with the Mini (the Micro mount lacks the holes for a zip tie). Too much unsupported mass slinging around for just the two holes on the Sherpa Micro to withstand. I managed to get the offset mount I was using before reprinted on another printer, so I can get the M1 back together and print out the Sherpa Mini parts. The other printer works in a pinch, but it's slow and the parts aren't as strong.

Closed 2023-09-10.

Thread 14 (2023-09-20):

Front modification for Ender 6 Usage?

RodentVienna, 2023-09-20:
Hi Jon!

First of all, THANK YOU for this project! I have been looking forever to find EVA3 compatibility for Ende 6. E34M1 is so very close.
I actually would like to ask, if there is a chance you would consider including a variant that directly allows compatibility for Ender 6.

the actual differences for Ender 6:
- Belts have teeth looking to the front, not to the back
- Belt mount compartments with slightly different position and dimensions.

By chance you would not have f3d files for the parts?

Alternatively I work out something myself and post the result as a remix on printables.com, but i thiought it may be  of interest to you, to officially add one more feature to the list - native ender 6 support.

Thank you!
Best regards, Alex

jon-harper, 2023-09-20:
I'm sorry, but making those modifications would be a large project, and I lack access to an Ender 6 for testing. 😢

You can find STEP files in the /CAD folder. Not all of them are entirely up to date, but they will work fine as a starting point for you.

RodentVienna, 2023-09-20:
Fair enough. After inspecting my situation further, my entire xy gantry requires rebuild anyway for this to make sense, as the ender 6 has its belts positioned around 30mm lower from the x_2020 profile, so that appears not compensatable even by the cleverest redesign of the FRONT part :)

Closed 2023-09-20.

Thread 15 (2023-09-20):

Top modification for sensorless homing

RodentVienna, 2023-09-20:
Hi Jon,

would you be interested in officially supporting sensorless Homing for X by providing another TOP part without compartments for microswitched?

Thank you!
Best, Alex

jon-harper, 2023-09-20:
The space for the limit switch can be left empty if you want to use sensorless homing.

I've seen [a modification on Printables](https://www.printables.com/model/333807-eva-3-sensor-less-homing-top-for-mgn9) that adds extra zip tie anchors where the X limit switch normally goes. Is this similar to what you're thinking?

RodentVienna, 2023-09-20:
Hi Jon, thank you for your support!
Yes, this is it, but for mgn9h instead of mgn12h.
I looked up printables.com, found 2 models for mgn12h, both without the mirrored zip-tie mount compartments. Having such as "official" alternative part from your project would be awesome. But i'd understand it will end up for you in "one more part to think of and support".
I guess i am fine with grabbing one of those mgn12h adaptions on printables, cut it in half, mirror the duplicated ziptie half and merge them back to a solid piece. Thank you!

jon-harper, 2023-09-20:
E34M1 is generally only compatible with EVA 3 hotends and drives. If your build is going to be compatible with E34M1, start with the [/CAD/Top](https://github.com/jon-harper/E34M1/tree/main/CAD/top) folder. I've updated the files there with the latest for you.

Part of the reason I'm hesitant to implement this is that the halves of the E34M1 Top piece are not symmetrical, so it would take more work to implement than cut-and-mirror.

The wire anchor is also next to the X limit switch mount and would have to be removed, as well. See below for a visual:

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

jon-harper, 2023-10-22:
I pinged you in Discord, but I've added this.

https://github.com/jon-harper/E34M1/blob/main/STL/top/top_no_endstop.stl

Closed 2023-10-22.

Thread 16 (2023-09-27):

Dragon UHF fit test

jon-harper, 2023-09-27:
I've added to `testing` a mount for the Phaetus Dragon UHF. Link to STL is in the BOM below.

**Bill of Materials**

| Parts     | Qty |
|-----------|-----|
| [`hotend_dragon_uhf.stl`](https://github.com/jon-harper/E34M1/blob/testing/STL/hotend/hotend_dragon_uhf.stl)  | 1 |
| Phaetus Dragon UHF            | 1 |
| Fan, 40mm x 10mm              | 1 |
| M2.5-0.45 x 8mm SHCS          | 4 |
| M3-0.5 x 6mm SHCS             | 4 |
| M3-0.5 x 12mm SHCS            | 4 |
| Heat Set Insert, M3x5x4       | 8 |

jon-harper, 2023-10-10:
Closing this, as multiple folks are running this version.

Closed 2023-10-10.

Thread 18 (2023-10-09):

Rapido UHF support

jon-harper, 2023-10-09:
I have the hotend model but still need to drop it in CAD and modify the regular Rapido model for UHF

jon-harper, 2023-10-31:
Per user reports in Discord, this is the wrong height. I've raised the hotend mount 1mm.

https://github.com/jon-harper/E34M1/commit/def74fd2971c033b8f3db34ac57aae5839ccd39a

jon-harper, 2023-11-17:
Seems to be working. Closing this out.

Closed 2023-11-17.

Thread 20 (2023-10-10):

Dual 5015 Flow4enol style

jon-harper, 2023-10-10:
Try making a rear inlet with the 5015 fans laid with their flat faces towards the X extrusion

jon-harper, 2023-11-17:
Seems to work, need docs.

jon-harper, 2023-11-29:
Added

Closed 2023-11-29.

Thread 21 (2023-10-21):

Widen 45mm screw holes for bottom horns

jon-harper, 2023-10-21:
Since the bottom horns are printed upright, 3.3mm is too tight a bore for the screws. This forces the user to thread them manually, which is frustrating. Widen to 3.6mm.

jon-harper, 2024-12-30:
Fixes were integrated awhile ago and neglected to close this.

Closed 2024-12-30.

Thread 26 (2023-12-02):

Why?

JonasV328, 2023-12-02:
I'm sorry if this is a stupid post.
Thank you for creating this thing. I'm thinking about building a Mercury Ony.1. Going through the documentation I had one question:
Why is this even needed? What did you have to change from the original EVA3 to make it compatible with Mercury One.1? Why could one not simply use the original EVA3? Is there a page where this is explained?

Thank you!

jon-harper, 2023-12-02:
Quite a few things changed.

The biggest issues was that Mercury One uses stacked belts, so that all four belt ends are in front of the X axis extrusion. EVA specifies that belts should go in front and behind the extrusion. Changing that led to other changes, such as reworking the entire back of EVA to remove the built-in belt tensioner.

After I got it working, I redesigned all of the parts to reduce weight, use the same heat set inserts that Mercury One uses, and so on. Hotends and extruder mounts are compatible with EVA 3, but otherwise it's a new toolhead.

Closed 2024-01-05.

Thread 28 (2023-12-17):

CRTouch UHF Mount

121Jigawatt, 2023-12-17:
The CRTouch mount for both the UHF and the non UHF look to be the same model unless i'm missing something.
Was that a mistake or does it use the same mount?

jon-harper, 2023-12-17:
Ack, this is definitely a mistake. There was an issue with the CR Touch model that needed fixing, but this looks like a simple 'oops'.

I will try to get a fixed UHF mount to you today.

121Jigawatt, 2023-12-17:
Thanks so much! Also I have made an edit that allows for this filament cutter to be used with the rapido on your E34M1 tool head.
https://www.printables.com/model/647352-filament-cutter-for-eva3-orbiter-rapido/files
I'm new to using github so what would be the best way to get the stls to you if you want them?
Our would you rather add a link to the printables page when I upload it?

jon-harper, 2023-12-17:
> Thanks so much! Also I have made an edit that allows for this filament cutter to be used with the rapido on your E34M1 tool head. https://www.printables.com/model/647352-filament-cutter-for-eva3-orbiter-rapido/files I'm new to using github so what would be the best way to get the stls to you if you want them? Our would you rather add a link to the printables page when I upload it?

That is a really neat design! Unfortunately, the modified Front makes it incompatible with E34M1. :-/

What about a thin spacer between hotend and extruder mount? Is that too high up to cut?

121Jigawatt, 2023-12-17:
It could definitely be done but at the cost of more wasted filament purge :/
The link that I sent was what I based it off of I edited your design to make it fit. I did have to remove the top font right extruder mounting hole to make it fit unfortunately. Cuts it right at the top of the heatsink. I getcha though, kinda takes away the whole modular design of the whole system. Thanks for looking at the abl mount though!
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

jon-harper, 2023-12-17:
> It could definitely be done but at the cost of more wasted filament purge :/ The link that I sent was what I based it off of I edited your design to make it fit. I did have to remove the top font right extruder mounting hole to make it fit unfortunately. Cuts it right at the top of the heatsink. I getcha though, kinda takes away the whole modular design of the whole system. Thanks for looking at the abl mount though! ![20231217_015811](https://private-user-images.githubusercontent.com/125784340/291051743-c76b7802-6318-4e92-a06f-a8b92c998a63.jpg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)

Oh my, I did not catch that. Color me more interested. If you have Discord, consider dropping by the ZeroG EVA 3 channel and spreading the word. I know *several* users who might be interested. Meanwhile, I'll share your printables link.

121Jigawatt, 2023-12-17:
Will do! I thought that might have been the case lol. Working on a way to actuate the cutting element with something similar to the X axis stop so I won't post anything until I get that worked out hopefully early next week

jon-harper, 2023-12-17:
There's a new `abl_crtouch_uhf.stl` file. Let me know if you run into any other issues.

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

And don't be a stranger if you want to punt ideas around! :-)

121Jigawatt, 2023-12-17:
Thanks! What's the best way to contact you, in that discord I'm guessing?
Also what is that bottom design, it looks awesome

jon-harper, 2023-12-17:
> Thanks! What's the best way to contact you, in that discord I'm guessing?

I tend to keep the ZeroG Discord open a lot, yeah.

> Also what is that bottom design, it looks awesome

That's Kraken. https://github.com/jon-harper/E34M1/tree/testing/STL/bottom It's been in testing, but is ready for release. I'm working on the docs this weekend. :-)

121Jigawatt, 2023-12-17:
Is it the Toolhead channel or is there a dedicated EVA3 channel that I'm not seeing?

jon-harper, 2023-12-17:
> Is it the Toolhead channel or is there a dedicated EVA3 channel that I'm not seeing?

It's a little hidden. Right here: https://discord.com/channels/747612067951018075/1041406799342997544

Closed 2023-12-17.

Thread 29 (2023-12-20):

Bottom horns for Rapido HF vs Rapido UHF

NikolaCv, 2023-12-20:
Greetings!

I've recently noticed a change in the design of the Rapido hotend mount, which now comes in two versions – one for HF and the other for UHF that allows for a slightly higher hotend mount (1.6mm). However, if (picture below) the UHF hotend is only compatible with UHF bottom horns when using the UHF hotend mount (and HF only with HF parts), it means that switching from HF to UHF needs changing both the bottom horns and the hotend mount, instead of just changing the horns. This adds the extra step of unscrewing the hotend itself, making the process more time-consuming.

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

Is it possible to revert to a single mount for both Rapido HF and UHF? Or does it even matter, since it's just a 1.6mm difference? I haven't printed the parts yet, so I don't know what's the height clearence from the nozzle tip to the bottom of the horns etc.

Any insights on this would be appreciated!

jon-harper, 2023-12-20:
EVA specifies the height of a nozzle should be, because the ducts have to
point at them. The hotend mount isn't there just to hold the hotend in
place: it also puts it at the right height for those ducts.

The 1.6mm difference between the two mounts is to get the Rapido UHF to the
right height for a UHF hotend.

Hope that explains why the Rapido and Rapido UHF don't share a mount.

- Jon

On Wed, Dec 20, 2023, 2:39 PM Nikola Cvetanovic ***@***.***>
wrote:

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

NikolaCv, 2023-12-20:
>The hotend mount isn't there just to hold the hotend in
place: it also puts it at the right height for those ducts.

Why not simply lower the ducts by 1.6mm instead of introducing a new hotend mount for UHF? Given that UHF requires a new Z offset and ducts anyway (roughly 9mm difference), adjusting the mount by 1.6mm doesn't maintain the nozzle at the same height.

jon-harper, 2023-12-21:
The Rapido UHF mount is the height it is because it conforms to the EVA 3
specification. I can't change this, as I did not create the spec.

On Wed, Dec 20, 2023, 5:41 PM Nikola Cvetanovic ***@***.***>
wrote:

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

NikolaCv, 2023-12-21:
What would be the problem if I used Rapido UHF with HF hotend mount, and modified the UHF ducts to match the nozzle height properly (make them point 1.6mm lower)? I genuinely don't see why this wouldn't work.

jon-harper, 2023-12-21:
It probably would work, but it wouldn't conform to the EVA spec anymore. Also ABL might be an issue if not also adjusted.

Closed 2023-12-28.

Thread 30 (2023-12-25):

Belt alignment

53Aries, 2023-12-25:
I'm seeing some pretty bad belt alignment from the front PIS v0.5. I haven't checked other front's to know if the issue is throughout.  Just wanted to make you aware either way. Thanks.
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

53Aries, 2023-12-25:
Oops sorry. Just spotted my error in connections. Disregard.

Closed 2023-12-25.

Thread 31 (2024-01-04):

Orbiter 2 does not have space for lock washers

jon-harper, 2024-01-04:
I missed this modification to the original; while I'm at it, should check the others for the same mistake.

zephyr2206, 2024-04-29:
What is this modification? Will the Orbiter 2 work with the heat inserts? Not sure what lock washers this is about.

jon-harper, 2024-04-29:
> What is this modification? Will the Orbiter 2 work with the heat inserts? Not sure what lock washers this is about.

If you aren't using lock washers, the Orbiter 2 drive module will work without a problem. I believe this is also fixed and I simply forgot to close the issue.

Closed 2024-04-29.

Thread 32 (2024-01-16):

Standard Kraken mounting holes are off

jon-harper, 2024-01-16:
Reported by Discord user MXJ1. Holes are off by 0.2 on the right side, center hole is off-center by 0.1, most likely (I'm eyeballing).
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

This hasn't affected user installs yet, so it's not a show-stopper. Still needs fixing, though.

jon-harper, 2024-02-07:
This is fixed with Kraken 0.6

Closed 2024-02-07.

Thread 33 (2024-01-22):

Owl-eyes duct - Beacon compatibility (also error with normal duct)

Ixian, 2024-01-22:
Any chance we could get a version of the Owl-eyes duct that has a Beacon compatible inlet like the single-duct version does?

Also, the download link for the standard Owl-eyes is broken - the .stl at the end of the link is missing the L. Simple fix but might throw some users off when they see the 404 pop up if they don't double-check the url.

Thanks for the work on the E34M1!!

jon-harper, 2024-01-22:
Fixed the URL, thanks. I've assigned the Beacon compatibility to get done later when I have time. :-)

Closed 2025-03-05.

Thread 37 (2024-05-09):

Dragon UHF "bottom horns" clarification

grilparto, 2024-05-09:
Not sure if this technically fits as an issue, but I wanted to encourage a minor clarification to the Dragon UHF Bottom Horn recommendations in the Intro Guide (https://jon-harper.github.io/E34M1/guide/) and the general notes for the Dragon UHF hotend mount (https://jon-harper.github.io/E34M1/modules/hotend/).

Context:  There are two possible configurations for the Dragon UHF.  One involves threading the nozzle directly into the heat block.  This configuration is not really capable of the "UHF" flow rates, instead it's on par with the HF version of the hot end.  The other configuration is to thread on an extension nut to the heatblock, and then thread the nozzle into the extension nut (Phaetus refers to it on the product page as an "extended nut".  The extension nut acts as an extended melt zone--functionally similar to a volcano hotend--allowing for the increased UHF flow rates.  The Rapido UHF appears to have the same configuration options (the user can choose to forgo the extension nut if they don't need the added flow rate).  Not sure why people seem to be commonly forgoing the extension nut on the Dragon UHF but not the Rapido UHF, but I digress.

The clarification: In any case, the first configuration works with the Dual or Kraken bottom horns as stated in the documentation.  However!  The second configuration does require the UHF or Kraken UHF bottom horns like the Rapido UHF.  I don't have the Rapido UHF to check, but I would assume that the same logic should also apply to the Rapido UHF if the user chooses to remove the extension nut.

jon-harper, 2024-05-14:
Have you tried testing this with the UHF horns to see if it's the correct height with the melt zone extension?

grilparto, 2024-05-14:
> Have you tried testing this with the UHF horns to see if it's the correct height with the melt zone extension?

Visual inspection, it looks like the air would be directed towards the nozzle correctly, but I still haven't done a functional test yet.  The non-UHF would aim at the base of the heater block, the UHF reaches the nozzle.  I can take a photo of it when I get back home.

Once I finish getting this all wired up and running again, I can report back on a functional test. Is there a specific way that I ought to test this?  I generally just check to see if airflow is at the nozzle tip, but not so low that it significantly disrupts the path of the extruded filament.  I've also tried using a small bowl or dish of water to get an idea of where the air starts to hit vs the nozzle height, but I don't know off-hand if there's a hard/fast rule I should conform to.

jon-harper, 2024-05-23:
The bottom of the horns should be about 1mm above the nozzle. If it's more than that you may run into issues.

grilparto, 2024-05-25:
> The bottom of the horns should be about 1mm above the nozzle. If it's more than that you may run into issues.

Oof!  Sorry, been engrossed with several hobbies this week.  Forgot to post a picture.

Looks like it's about 1-1.5mm above the nozzle tip, so probably ok.  Hard to measure with the calipers or without a feeler gage, but I kind of used a tweezers as a compass and then measured the tweezers gap with a ruler.  I did a quick PLA print yesterday (because I needed a widget for one of my other hobbies) and it seemed to work fine.  It was a pretty tame object though so I'll have to put it through its paces to see if the positioning is adequate for bridging and overhangs.

Here's a pic from a week ago:

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

jon-harper, 2024-05-25:
It's hard to judge the height from a picture, but I'll trust your results.
Can you do a benchy and see how the bow looks? Don't rotate the model.

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

jon-harper, 2024-05-29:
No worries. I appreciate you following up.

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

grilparto, 2024-05-30:
Suppose I should mention a couple of confounding factors to preface these photos.  I'm printing with a 0.6mm nozzle, and using a tent enclosure.  Both present some interesting challenges when it comes to printing a Benchy (or anything small).  Which is to say that it's like drawing fine detail with a magic marker and cooling pla with hot air.  Also didn't help that I forgot to reposition the seam to a corner.  In any case, the results pretty much align with what I've had to deal with/workaround in the past.

Layer height was 0.3mm.  For the most part, for the better print, the print speed was around 60mm/s (give or take depending on layer time).  For the "fast" print, it was 100mm/s (again, give or take).  I'm debating about swapping out for the 0.4 nozzle and trying again but I don't generally print with that on the larger Ender 5 Plus anyway.

The main problems encountered are ones I'd generally attribute to not being able to cool the filament fast enough.  Is it the duct's fault?  I'm not overly convinced since I'd been grappling with similar issues with an adjustable height duct previously.  I'm more inclined to believe that the single 5015 fan and the ambient heat in the chamber are mostly responsible.  Additionally, I think the water test results I also included below are convincing enough for me to accept the duct height.  I think the dimple could be _little_ flat which might suggest that the fan is a shade higher than ideal, but it's still hitting the layer being printed and several under it.

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

For the water test below, I leveled the nozzle tip with the water and then adjusted the fan speed for 25%, 50%, 75%, and 100%.

(First one is 0%)
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

jon-harper, 2024-05-31:
I designed the Kraken duct to work around concerns regarding the direction of airflow with the stock dual horns. EVA has an unresolved issue about this: https://github.com/EVA-3D/eva-main/issues/117 I apologize for not mentioning the EVA issue sooner; I just remembered it.

Kraken is not perfect, but it does give more uniform distribution of air than the dual horns. You might try it, even if only for comparative purposes.

On Thu, May 30, 2024, 1:19 PM grilparto ***@***.*** ***@***.***> > wrote:

Suppose I should mention a couple of confounding factors to preface these photos. I'm printing with a 0.6mm nozzle, and using a tent enclosure. Both present some interesting challenges when it comes to printing a Benchy (or anything small). Which is to say that it's like drawing fine detail with a magic marker and cooling pla with hot air. Also didn't help that I forgot to reposition the seam to a corner. In any case, the results pretty much align with what I've had to deal with/workaround in the past.

Layer height was 0.3mm. For the most part, for the better print, the print speed was around 60mm/s (give or take depending on layer time). For the "fast" print, it was 100mm/s (again, give or take). I'm debating about swapping out for the 0.4 nozzle and trying again but I don't generally print with that on the larger Ender 5 Plus anyway.

The main problems encountered are ones I'd generally attribute to not being able to cool the filament fast enough. Is it the duct's fault? I'm not overly convinced since I'd been grappling with similar issues with an adjustable height duct previously. I'm more inclined to believe that the single 5015 fan and the ambient heat in the chamber are mostly responsible. Additionally, I think the water test results I also included below are convincing enough for me to accept the duct height. I think the dimple could be little flat which might suggest that the fan is a shade higher than ideal, but it's still hitting the layer being printed and several under it.

PXL_20240530_151948875.RAW-01.COVER.jpg (view on web) <https://github.com/jon-harper/E34M1/assets/82681495/a36e7dc3-7ddf-4c4b-9912-5781d4486db5>
PXL_20240530_164616238.RAW-01.COVER.jpg (view on web) <https://github.com/jon-harper/E34M1/assets/82681495/9034e676-58c5-4955-b407-440c2b7d0847>
PXL_20240530_164626281.RAW-01.COVER.jpg (view on web) <https://github.com/jon-harper/E34M1/assets/82681495/71844d02-01a3-442a-b40a-fdf18580f2fe>
PXL_20240530_164636591.RAW-01.COVER.jpg (view on web) <https://github.com/jon-harper/E34M1/assets/82681495/ae311801-42da-4462-b212-1f9dde48067f>
PXL_20240530_164653775.RAW-01.COVER.jpg (view on web) <https://github.com/jon-harper/E34M1/assets/82681495/c6bd013c-89b3-4973-bf8a-c424c3ee3713>

For the water test below, I leveled the nozzle tip with the water and then adjusted the fan speed for 25%, 50%, 75%, and 100%.

(First one is 0%)
PXL_20240530_180101279.RAW-01.COVER.jpg (view on web) <https://github.com/jon-harper/E34M1/assets/82681495/30d83eb2-cc0a-4b05-9fe6-3ae683fd73bb>
PXL_20240530_180125951.RAW-01.MP.COVER.jpg (view on web) <https://github.com/jon-harper/E34M1/assets/82681495/d22a6018-ec73-4ce9-9308-0f28f6b1819c>
PXL_20240530_180223350.RAW-01.MP.COVER.jpg (view on web) <https://github.com/jon-harper/E34M1/assets/82681495/77b136ee-ade9-42ba-a348-76f55804a8ce>
PXL_20240530_180258103.RAW-01.MP.COVER.jpg (view on web) <https://github.com/jon-harper/E34M1/assets/82681495/4de73240-f60f-4100-8fb3-4e81c5d44feb>
PXL_20240530_180413166.RAW-01.MP.COVER.jpg (view on web) <https://github.com/jon-harper/E34M1/assets/82681495/50b95fc4-4f2f-4a77-a1d9-75dfc9d838d1>

—
Reply to this email directly, view it on GitHub <https://github.com/jon-harper/E34M1/issues/37#issuecomment-2140550261> , or unsubscribe <https://github.com/notifications/unsubscribe-auth/AC2NUY7O7C5P7MVSMOPWBP3ZE5USRAVCNFSM6AAAAABHN6NDLKVHI2DSMVQWIX3LMV43OSLTON2WKQ3PNVWWK3TUHMZDCNBQGU2TAMRWGE> .
You are receiving this because you commented.  <https://ci3.googleusercontent.com/meips/ADKq_NbuUuRVTXvJ8kUF9qMl9QEmLOjhexjIH00idf3xSADu3awSv97TAWIEuUkYDeqUo3MnFvLxo9ER6HngiFaRIZwq8HNZq4a3q7kvTHf7lcwWTi66NjdrWDEoV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> Message ID: ***@***.***>

grilparto, 2024-05-31:
> I designed the Kraken duct to work around concerns regarding the direction of airflow with the stock dual horns. EVA has an unresolved issue about this: [EVA-3D/eva-main#117](https://github.com/EVA-3D/eva-main/issues/117) I apologize for not mentioning the EVA issue sooner; I just remembered it.

No worries!  So, the stock duct with the 5015 fan puts the air in front of the nozzle a little instead of under it?  Interesting.  I can give the Kraken a try.  I just printed a dual 5015 inlet and was also looking at the CPAP one (but I don't think the E5Plus stock PSU can handle the cpap fan's power consumption while the rest of the system is under full load).

jon-harper, 2024-07-23:
How did this turn out for you? Did Kraken work better?

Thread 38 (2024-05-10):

top_left_microswitch.stl incompatible with drive_bmg.stl - Not enough clearance for cable anchor

grilparto, 2024-05-10:
When integrating the  top_left_microswitch.stl with drive_bmg.stl, there is not enough clearance to install the cable anchor due to the NEMA17 motor's size.  The only workaround is to remove the cable anchor.  My fusion360 skills are currently awful, but if I manage to come up with a modded design, I'll include it here.

grilparto, 2024-05-10:
Came up with an offset version that should fit with the BMG/NEMA17 configuration.  It fits around the NEMA17 and I also added a boot heel (draft, or whatever it's technically called) so that the anchor doesn't spin around in place.  The mount point for the anchor on the top_left_microswitch.stl is flush with the rest of the top surface, so there was nothing to prevent the original anchor design from spinning in place.

Old design: 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

Modified design: 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

And here it is installed: 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

grilparto, 2024-05-10:
Suppose attaching the STL file would also be useful.  Given the limits on filetypes that can be upload, anyone grabbing this will need to change the .txt extension to .stl.

[cable_anchor-nema17offset.txt](https://github.com/jon-harper/E34M1/files/15279294/cable_anchor-nema17offset.txt)

jon-harper, 2024-05-14:
This is very cool work! Thank you for both reporting this *and* solving it.

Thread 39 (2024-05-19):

Ender5S1 hotend

oresk, 2024-05-19:
From what I understand there is already a way to mount the extruder from Ender5S1. It would be really great if there would be mounts for the "default" hotend too.

Thnx for all the great work!

jon-harper, 2024-05-23:
I don't see a compatible mount on Printables. You might see if anyone's made one on the RatRig Discord server, perhaps?

If you find one, lmk and I'll add it to the docs.

Closed 2024-05-23.

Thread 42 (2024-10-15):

User contribution:  ABL Side Mounts for BTT Microprobe

wagnerism, 2024-10-15:
I'm offering my Standard and UHF mounts for the BTT MicroProbe in STL format. I have personally tested both files with both Rapido HF and Rapido UHF hot ends.

I'd create a PR but I don't know how to create pictures consistent with what you have already.

I intentionally put the wire on the outside because I prefer a smaller probe X offset over hiding the wire and making it difficult to connect.

[abl_btt_microprobe_standard_and_uhf.zip](https://github.com/user-attachments/files/17381986/abl_btt_microprobe_standard_and_uhf.zip)

jon-harper, 2024-12-30:
Thanks! I'll get to work on this. Apologies for the delay.

wagnerism, 2025-02-06:
No worries.  Thank you for your work here. I'm glad to contribute in some small way.

3D-Experiments, 2025-03-02:
The UHF version seems to be the right size for my set up. I'll post some results after testing. In the meantime, I've adjusted the orientation of the STLs to obviate supports.

[abl_btt_microprobe_standard_and_uhf-NO-SUPPORTS-ORIENTATION.zip](https://github.com/user-attachments/files/19041228/abl_btt_microprobe_standard_and_uhf-NO-SUPPORTS-ORIENTATION.zip)

3D-Experiments, 2025-03-02:
Mounted height looks correct for my set up...

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

jon-harper, 2025-03-17:
This is really good stuff. Thank you both. What kind of hardware does this need? 2 inserts and 4x M3x6mm?

3D-Experiments, 2025-03-18:
M3X6 worked for me but I'll defer to @wagnerism to confirm.

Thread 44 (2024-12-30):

TriangleLabs TD6S hotend mount. STL and STEP enclosed

53Aries, 2024-12-30:
Just figured I'd dump this here if you want to add it.

[HOTEND_TD6S.zip](https://github.com/user-attachments/files/18273406/HOTEND_TD6S.zip)
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

jon-harper, 2025-03-05:
Checking that the values below are correct:

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

53Aries, 2025-03-05:
> Checking that the values below are correct:
>
> 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

Looks correct to me. Here's my full assembly that I've been using if you need to check anything. Thanks

[TD6S Assembly.zip](https://github.com/user-attachments/files/19095259/TD6S.Assembly.zip)

jon-harper, 2025-03-05:
I've pushed an update to the docs including the TD6S. Thanks for contributing. :-)

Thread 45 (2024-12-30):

Owleyes rear inlet fix. STL and STEP enclosed

53Aries, 2024-12-30:
Made some adjustments to the owleyes to hopefully let air move more freely to all the ducts.
Before:
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
After:
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
[rear_dual_5015_owl_eyes_fixed.zip](https://github.com/user-attachments/files/18273424/rear_dual_5015_owl_eyes_fixed.zip)

jon-harper, 2024-12-30:
I appreciate the contribution, but without a CFD analysis, there's not a good way to tell which version will be more efficient. Your version has increased volume, but may cost in terms of added turbulence from the screw bypasses.

There is probably a very good compromise between the two with a thinner "rib" below the screw holes, but at the moment I can't justify choosing one or the other.

Closed 2024-12-30.

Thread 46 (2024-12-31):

kraken_klicky very minimal clearance between klicky mount and printer bed

53Aries, 2024-12-31:
Just switched to kraken klicky from trihorn klicky and found out the klicky mount portion of kraken is waaaaay close to the bed. .155mm to be exact. Just figured if you still have the project file it might be easy to bump the klicky module up like 1mm. I'll work on it also.
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
a

jon-harper, 2024-12-31:
what hotend is this?

jon-harper, 2024-12-31:
I'm not sure what the issue is with clearance. Are you concerned about weakening magnets?

53Aries, 2024-12-31:
> I'm not sure what the issue is with clearance. Are you concerned about weakening magnets?

It's probably just a me thing. I like having 2mm or more clearance just to avoid hitting curled perimeters, and to avoid my nozzle brush and purge bucket servo.

jon-harper, 2024-12-31:
That's fair enough. Let me see how hard the file will be to modify.

jon-harper, 2024-12-31:
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
[kraken_klicky_2mm.zip](https://github.com/user-attachments/files/18282985/kraken_klicky_2mm.zip)

Try this. 2mm offset to build plate.

53Aries, 2024-12-31:
Thanks. Can I get a .step to update my cad model?

jon-harper, 2024-12-31:
[kraken_klicky_2mm_step.zip](https://github.com/user-attachments/files/18283149/kraken_klicky_2mm_step.zip)

Not a problem. Let me know how this goes and I'll add it to the repo/docs.

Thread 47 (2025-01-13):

MGN9 for x axis

oresk, 2025-01-13:
Any particular reason not to use a MGN9 rail for the x axis?

Also anybody saw a top plate for it ?

jon-harper, 2025-01-13:
Single MGN9 works well only for smaller build sizes, like the V.0. Older Vorons used dual MGN9 rails, but have since switched to single MGN12.

Closed 2025-01-13.

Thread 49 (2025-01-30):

D2HW Filament Sensor

jon-harper, 2025-01-30:
https://www.printables.com/refresh?redirectUrl=%2Fmodel%2F1170113-eva-30-d2hw-filament-sensor

jon-harper, 2025-03-05:
Added.

Closed 2025-03-05.

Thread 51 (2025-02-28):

Correct Printing Orientation?

3D-Experiments, 2025-02-28:
https://github.com/jon-harper/E34M1/blob/main/STL/top/top_left_microswitch.stl

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

and

https://github.com/jon-harper/E34M1/blob/main/STL/top/top_right_microswitch.stl

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

have different printing orientations.

Does https://github.com/jon-harper/E34M1/blob/main/STL/top/top_right_microswitch.stl need to be flipped to avoid supports?

jon-harper, 2025-02-28:
Ooh good find. Yes, that should be flipped.

On Thu, Feb 27, 2025, 7:58 PM 3D Experiments ***@***.***>
wrote:

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

jon-harper, 2025-03-05:
Fixed. Thanks.

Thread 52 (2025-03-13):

Sherpa Mini HSI locations missing

jon-harper, 2025-03-13:
Materials page for Sherpa Mini does not mention HSI for the mount.

Closed 2025-03-17.

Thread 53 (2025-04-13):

E34M1 Beacon_Bottom_UHF Not Compatible with Beacon Low Profile Rev H

iblueup, 2025-04-13:
Beacon Rev H has components on the top of the PCB that result in a tilt of the scanner when mounted to the mentioned duct.

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

I temporarily resolved this by removing material post-printing.

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

A fix for this is made for standard EVA 3, by shortening the mounting boss to clear SMDs, but this does not fit the E34M1 spacing between front and rear.
https://www.printables.com/model/865950-eva-3-beacon-revh-uhfvolcano

Any help to adjust the E34M1 duct to accommodate Rev H are appreciated!

jon-harper, 2025-04-13:
Thanks for the report. The easiest fix is to split the Rev D and Rev H models, I think.

iblueup, 2025-04-16:
Thanks for the attention on this! Looking at all the bottom duct options, I can imagine it'll take some effort.

Really appreciate you making such a wonderful project available and continuing to support it!!

jon-harper, 2025-04-17:
By the way, you can use the Kraken UHF as-is with any Beacon rev, just update the Y offset.

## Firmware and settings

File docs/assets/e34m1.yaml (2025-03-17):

config:
  id: test
  baseUrl: https://raw.githubusercontent.com/jon-harper/E34M1/main
suppliers:
  3do:
    name: 3DO
    region: EU (DK)
    ships: EU
  aliexpress:
    name: AliExpress
    region: Worldwide
    ships: Worlwide
  amazon_us:
    name: Amazon.com (USA)
    region: US
    ships: US
  bolt_depot:
    name: Bolt Depot
    region: US
    ships: US
  digikey:
    name: Digikey
    region: Worldwide
    ships: Worldwide
  fabreeko:
    name: Fabreeko
    region: US
    ships: Worldwide
  stepperonline:
    name: StepperOnline
    region: Worldwide
    ships: Worldwide
  3djake:
    name: 3DJake
    region: EU (AT)
    ships: Worldwide
  kb3d:
    name: KB-3D
    region: US
    ships: Worldwide
  west3d:
    name: West3D
    region: US
    ships: Worldwide
  biqu:
    name: Biqu/Bigtreetech
    region: CN, US, EU, CA
    ships: Worldwide
  tinymachines:
    name: Tiny Machines
    region: US
    ships: US
  filastruder:
    name: Filastruder
    region: US
    ships: US
  e3d:
    name: E3D Online Store
    region: UK
    ships: Worldwide
  beacon3d:
    name: Beacon3D Store
    region: US
    ships: Worldwide
  3dpassion:
    name: 3D Passion
    region: Unknown
    ships: Unknown
  th3d:
    name: TH3D
    region: US
    ships: Unknown
authors:
  u_cuiviemen:
    name: cuiviemen
    url: https://www.printables.com/@cuiviemen_127292
  u_psychohead:
    name: Psych0h3ad
    url: https://www.printables.com/@Psych0h3ad_168275
  u_flow4enol:
    name: flow4enol
    url: https://www.printables.com/@Flow4Enol
  u_3dpandme:
    name: 3DP and Me
    url: https://www.printables.com/@3DPandMe
  u_eva:
    name: EVA
    url: https://main.eva-3d.page/
  u_etotheipi:
    name: etotheipi
    url: "https://www.printables.com/@etotheipi"
  u_themacboy:
    name: themacboy
    url: "https://www.printables.com/@themacboy_276431"
  u_jonspaceharper:
    name: jonspaceharper
    url: "https://www.github.com/jon-harper/"
  u_svennixx:
    name: Svennixx
    url: "https://github.com/Svennixx"
  u_pwnyourace:
    name: pwnyourace
    url: ""
  u_grilparto:
    name: grilparto
    url: "https://github.com/grilparto"
  u_3dexperiments:
    name: 3D Experiments
    url: "https://www.printables.com/@3DExperiments"
  u_53aries:
    name: 53Aries
    url: "https://github.com/53Aries"
parts:
  DIN 7981: # Self-tapping
    din7981_m2_8mm:
      name: Self-tapping M2 x 8mm Screw
      sources:
        amazon_us:
          url: https://www.amazon.com/uxcell-Stainless-Phillips-Tapping-Screws/dp/B01M0P01I5
          note: 50pk

  DIN 125: # Washers
    washer_m3:
      name: M3 Washer
      sources:
        bolt_depot: 
          url: "https://www.boltdepot.com/Product-Details.aspx?product=4513"

  DIN 127: # Lock Washers
    lock_washer_m3:
      name: M3 Split Lock Washer
      sources:
        bolt_depot:
          url: "https://www.boltdepot.com/Product-Details.aspx?product=4810"
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

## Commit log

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2023-04-03 Adding source files
    [5015_inlet_fi.step, 5015_inlet_fi.stl, 5015_sideways_inlet.step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]
2023-04-03 renamed files
    [hotend_dragon_bmo.stl, klicky_bottom.stl, pis_front.stl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]
2023-04-04 Added Beacon mounts
    [beacon_bottom.stl]
2023-04-04 Trihorn STEP files
    [Bottom - Trihorn.step]
2023-04-04 Added trihorn ducts
    [klicky_bottom_trihorn.stl, stock_bottom_trihorn.stl]
2023-04-05 STEP reorg
    [5015_inlet_fi.step, 5015_sideways_inlet.step, Bottom Horns - Volcano v1.step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]
2023-04-05 More renaming
    [core.step, front_intake_duct.step, pcb_mounts.step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]
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2023-04-08 Fix the STL oops
    [belt_grabber.stl, bl_touch_mount.stl, bl_touch_volcano_mount.stl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]
2023-04-08 Hopefully fix more oops
    [5015_inlet_fi.step, BLTouch.step, Front Intake Duct.step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]
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2023-04-11 Optimized sideways inlet
    [rear_5015_inlet_sideways.stl]
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2023-04-12 Phaetus hotends with Voron inserts
    [hotend_dragon_uhf.stl, hotend_dragonfly_bmo.stl, hotend_dragonfly_bms.stl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]
2023-04-12 Orbiter mounts with Voron inserts
    [drive_orbiter_1_5.stl, drive_orbiter_2_0.stl]
2023-04-13 Updated CR Touch mount
    [cr_touch_mount.stl]
2023-04-13 New Beacon STEP and rear inlet
    [rear_inlet_beacon.stl]
2023-04-13 Removed files committed too soon
    [hotend_dragon_uhf.stl, hotend_dragonfly_bmo.stl, hotend_dragonfly_bms.stl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]
2023-04-13 Fixed M2.5 holes
    [hotend_dragon_bmo.stl]
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2023-04-14 Added new hotends
    [hotend_dragonfly_bmo.stl, hotend_dragonfly_bms.stl, hotend_mosquito.stl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]
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2023-04-18 Added new Beacon files
    [beacon_bottom.stl, beacon_bottom_no_hsi.stl, beacon_bottom_trihorns.stl]
2023-04-18 Uploaded the correct version
    [rear_inlet_beacon.stl]
2023-04-18 Print orientation
    [beacon_bottom.stl, beacon_bottom_no_hsi.stl, beacon_bottom_trihorns.stl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]
2023-04-18 Print orientation; version number
    [beacon_bottom.stl, beacon_bottom_no_hsi.stl, klicky_bottom.stl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]
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2023-04-19 bom fix
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2023-04-20 Added screw cap
    [screw_cap.stl]
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2023-04-20 Fixed BOM entries for screws
2023-04-20 Fixed mixup
    [pis_front.stl, stock_front.stl]
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2023-04-22 Added step for stock intake adapter
    [stock_intake_adapter.step]
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2023-04-25 Added LGX Lite to main
    [drive_lgx_lite.stl]
2023-04-25 Added BMG mount to main
    [drive_bmg.stl]
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2023-04-28 Updated with Front v0.2
    [Core.step]
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2023-05-02 Dual 5015s
    [Dual 5015 Inlet.step, dual_5015_inlet.stl]
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2023-05-10 Fixed BLTouch mount
    [bl_touch_mount.stl]
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2023-05-28 Fixed missing commit
    [belt_grabber.stl, pis_front.stl, stock_front.stl]
2023-06-08 Print orientation & wider mouth
    [pcb_shroud.stl, pcb_shroud_30mm_fan.stl, pcb_shroud_cat.stl]
2023-06-08 Minor belt tweaks; PIS mount improvements
    [belt_grabber.stl, pis_front.stl, stock_front.stl]
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2023-07-29 Moved mount up 1.5mm
    [bl_touch_mount.stl]
2023-08-16 Added clearance for wires
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2023-09-03 Added Sherpa Mini from testing
    [drive_sherpa_mini.stl]
2023-09-04 Lighter dual horns (v0.2)
    [stock_bottom.stl]
2023-09-04 v0.2: reduced part weight
    [beacon_bottom.stl]
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2023-09-11 Update to 0.4 (new cable anchor)
    [cable_anchor.stl, top_endstop_left.stl, top_endstop_right.stl]
2023-09-11 Update with angled fans
    [dual_5015_inlet.stl]
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2023-09-11 Renamed to follow scheme
    [uhf_horns.stl]
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2023-09-20 Updated top CAD files
    [Top_right_handed.step, top_left_handed.step]
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2023-09-22 Updated dual inlet to latest
    [Dual 5015 Inlet.step]
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2023-10-22 Added sensorless homing top
    [top_no_endstop.stl]
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2023-10-22 Clarification and BOM fix
2023-10-29 Added LGX to main
    [drive_lgx.stl]
2023-10-29 Merging in 8mm probe mount
    [8mm_probe_mount.stl]
2023-10-29 Merging in to main
    [hotend_dragon_uhf.stl]
2023-11-02 Print orientation; removed stale file
    [stock_bottom.stl, stock_bottom_uhf.stl]
2023-11-03 Added Rapido UHF to main
    [hotend_rapido_uhf.stl]
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2023-11-13 Updated all CAD to latest
    [BLTouch.step, Bottom Horns.step, Dragon.step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]
2023-11-13 Updated STLs to R2
    [8mm_probe_mount.stl, abl_8mm_probe.stl, abl_bl_touch.stl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]
2023-11-13 fixed print orientation
    [belt_grabber.stl]
2023-11-16 taller stop block for X axis
    [taller_x_axis_stop_block.stl]
2023-11-24 adding missing drive module CADs
    [drive_bmg.step, drive_lgx.step, drive_lgx_lite.step]
2023-11-24 CAD cleanup; updated master file
    [Front Intake Duct.step, X Axis Stop Block.step, X Max Stop Block.step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]
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2023-11-27 Merging in Owl Eyes
    [rear_dual_5015_owl_eyes.stl]
2023-12-03 Fixed the belt grabber's grabbers
    [belt_grabber.stl]
2023-12-06 Corrected wire diameter
2023-12-09 Creality Sprite SE drive mount
    Made a Creality sprite SE drive mount, the extruder works fairly well for the price and comes on some of the newer creality printers including the Ender 5 S1 which I have and converted to Mercury One.1, didn't want to upgrade exturders just yet.
    [drive_creality_sprite_se.step]
2023-12-09 Creality Sprite SE Drive mount
    Made a Creality sprite SE drive mount, the extruder works fairly well for the price and comes on some of the newer creality printers including the Ender 5 S1 which I have and converted to Mercury One.1, didn't want to upgrade extruders just yet.
    [drive_creality_sprite_se.stl]
2023-12-12 Changed orientation to print orientation
    [drive_creality_sprite_se.stl]
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2023-12-17 Corrected height issues
    [abl_cr_touch.stl, abl_cr_touch_uhf.stl]
2023-12-18 Update top to 0.8
    [top_left_endstop.stl, top_left_endstop_anchor.stl, top_no_endstop.stl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]
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2023-12-18 Merging in new files
    [drive_orbiter_2_0.stl, dual_5015_owl_eyes.stl, rear_dual_5015_owl_eyes.step]
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2023-12-19 hsi images, typos, fixes
    [e34m1.yaml]
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2024-01-05 Added Kraken STEP files
    [kraken_beacon.step, kraken_klicky.step, kraken_stock.step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]
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2024-01-28 Probe offset fix
    [abl_8mm_probe_uhf.stl]
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2024-02-07 Added step; updated versions
    [kraken_klicky.step, kraken_stock.step]
2024-02-26 Top STEP files -> v0.8
    [top_left_endstop.step, top_left_endstop_anchor.step, top_no_endstop.step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]
2024-03-10 Fixed a bom typo
    [e34m1.yaml]
2024-03-11 Fix Flow4Enol URL
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2024-03-18 Fixed screw_cap.stl entries
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2024-04-09 fix typo in PCB mounts Douglas Adams
    fix 46 to 42 typo in 2 locations
    The answer to the universe and this pull request is ....
    42
2024-04-16 Added Beacon rev D and H universal bottoms
    [kraken_beacon.step]
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2024-04-16 Forgot to add CAD/bottom/stock_bottom_beacon.step
    [stock_bottom_beacon.step]
2024-04-30 Tweaks and version numbers
    [kraken_beacon.step]
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2024-07-23 BTT Eddy support
    Standard length, only ATM
    [abl_eddy.stl]
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2025-02-23 beacon owl eyes STEP
    [rear_dual_5015_owl_eyes_beacon.step]
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2025-03-05 Fixes PR by thbl
    [e34m1.yaml]
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2025-03-30 Improved airflow for the Mosquito hotend
    Redesigned the mounting bracket to duct into the cooling chamber rather than blow into the heatsink creating turbulence, and also went ahead and expanded the exhaust to help with airflow. I was getting really bad heat creep and redesigned the cooling portion of the mount.
    [hotend_mosquito_rw.stl]
2025-03-30 STEP file for the improved Mosquito mount
    Improved airflow for the heatsink.
    [RW Mosquito EVA3 Hotend.step]
2025-03-30 Update and rename RW Mosquito EVA3 Hotend.step to hotend_mosquito_osr.step
    [hotend_mosquito_osr.step]
2025-03-30 Mosquito cleanup & rename
    [hotend_mosquito_osr.stl]
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
